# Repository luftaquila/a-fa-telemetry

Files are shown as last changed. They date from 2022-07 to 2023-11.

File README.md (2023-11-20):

# 차량 원격 계측 시스템

> [!CAUTION]
> ⚠️ DEPRECATED<br><br>
> 이 저장소는 유지보수되지 않습니다.<br><br>
> 추가 업데이트 및 유지보수는 오픈소스 DIY 데이터로거 [monolith](https://github.com/luftaquila/monolith)에서 이루어지고 있습니다.

<hr>

상위 프로젝트: [luftaquila/a-fa-landing](https://github.com/luftaquila/a-fa-landing)

아주대학교 자작자동차소학회 A-FA의 E-Formula 차량용 데이터로거입니다.

### 기능
1. CAN 버스 트래픽 모니터링 (BMS 및 모터 컨트롤러 데이터)
2. 6채널 디지털 입력 신호 모니터링 (BMS / BSPD / IMD 오류, HV 활성화, RTD 활성화 신호)
3. 4채널 아날로그 입력 신호 모니터링 (서스펜션 변위 센서)
4. 4채널 디지털 펄스 모니터링 (휠 스피드 센서)
5. 3축 가속도 센서 데이터(I2C)
6. GPS 위치 정보(UART)
7. 자체 CPU 온도 모니터링
8. 무선 시간 동기화 및 RTC를 통한 시간 정보 유지
9. 드라이버 계기판 LCD 시현(I2C)
10. 수집한 데이터의 SD카드 로깅(SDIO/FATFS)
11. 수집한 데이터의 실시간 무선 인터넷 전송

### 디렉터리 구조
* device: 임베디드 MCU 펌웨어
    * ECU: 차량 데이터 수집용 STM32F4 STM32CubeIDE 프로젝트
    * ESP: 서버 소켓 통신용 ESP32 아두이노 프로젝트
* server: 원격 계측 서버 백엔드(Node.js)
* web: 원격 계측 모니터링 웹 어플리케이션 프론트엔드

### 회로도 및 PCB
[설계 파일](https://github.com/luftaquila/a-fa-schematics/tree/master/PCBs/LV_PCB%20v2)




## 서비스 URL
* [A-FA E-포뮬러 원격 계측 시스템](https://a-fa.luftaquila.io/telemetry)

screencapture-a-fa-luftaquila-io-telemetry-2023-08-26-16_22_42



## Log structure (16 Byte)
```c
typedef struct {
  uint32_t timestamp;
  uint8_t level;
  uint8_t source;
  uint8_t key;
  uint8_t _reserved;
  uint8_t value[8];
} LOG;
```

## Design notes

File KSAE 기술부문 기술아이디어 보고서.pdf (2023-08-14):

자동차공학은 한국의 힘! | 사단법인 한국자동차공학회

## 대학생 자작자동차대회

# 기술부문 신청서

학교명 | 아주대학교 | 팀명 | A-FA
지도교수 | 전용호 | 팀장 | 김병찬
차량 | 명칭 | A12
| 제원 | 길이 mm × 폭 mm × 높이 mm (무게 kg)
부문 | | ■ 기술아이디어 부문 □ 디자인 부문

상기 참가팀은 KSAE 대학생 자작자동차대회의 기술부문 (기술아이디어 및 디자인) 참가를 신청하며 다음과 같이 보고서를 제출합니다.

년 | 월 | 일

# 대학생 자작자동차대회 조직위원회 귀중

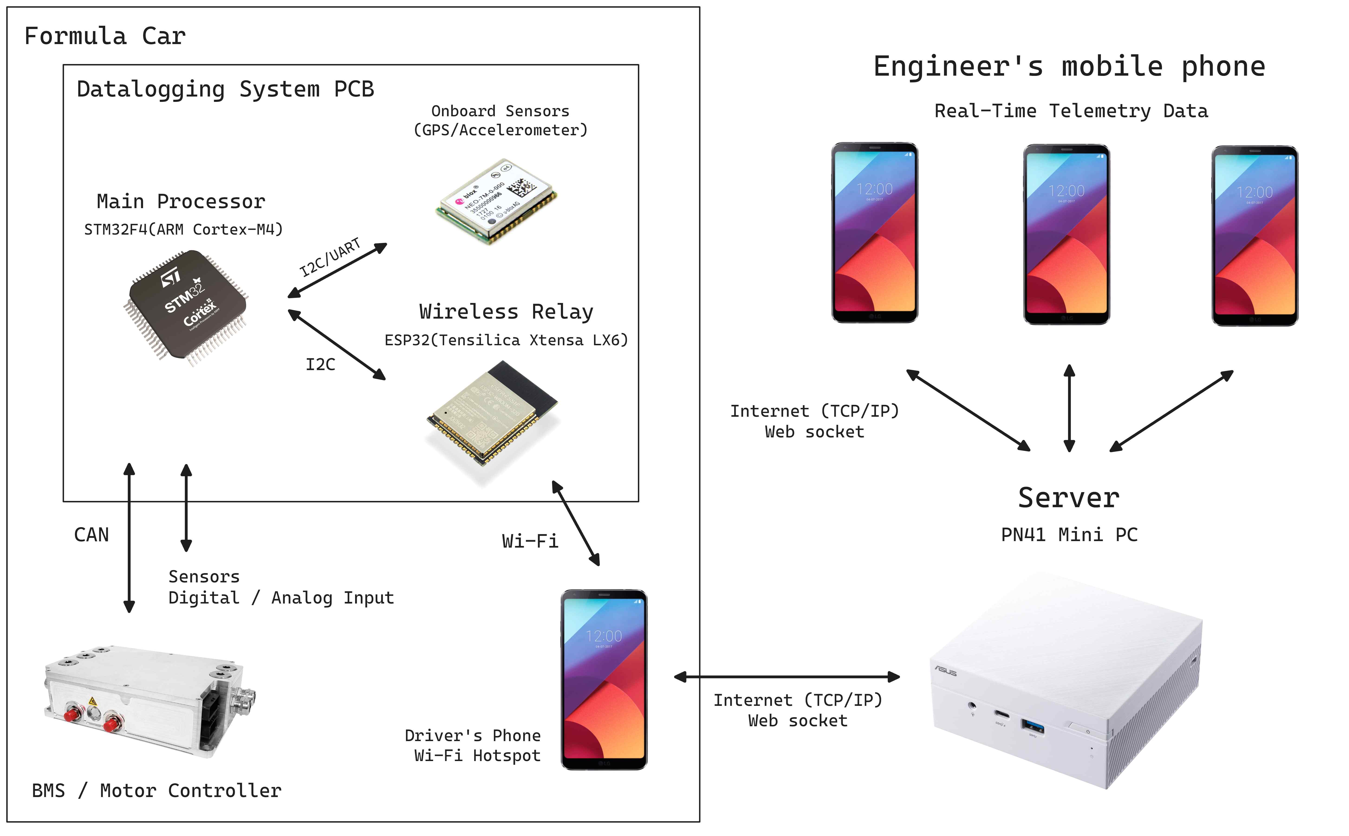
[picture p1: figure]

자동차공학은 한국의 힘! | 사단법인 한국자동차공학회

## 대학생 자작자동차대회

# 기술아이디어 보고서

￭ Summary
본 기술아이디어는 E-Formula 경주 차량의 주행 데이터 수집 및 실시간 원격 모니터링을 위한 임베디 드 하드웨어 및 소프트웨어 시스템이다. KSAE 출전과 같이 특수한 목적을 위해 개발하는 프로토타입 차량들은 제작 후 주행 성능 평가가 개발

과정에서 굉장히 큰 비중을 차지한다. 또한, 주행 중 예상치 못한 상황과 사고가 발생할 확률이 양산 차 량보다 훨씬 높다. 이러한 이유로 성능 평가, 사고 원인 분석 및 엔지니어링 등을 위해 차량의 주행 데 이터 수집은 반드시 필요하다. 그러나, 현재 찾아볼 수 있는 차량 데이터로깅 장비들은 그 성능과 기능 이 파편화되어 있어 하나의 장비로 개발팀의 모든 요구사항을 만족시키기 어렵다. 따라서, 하나의 데이 터로깅 플랫폼에서 CAN 트래픽, Real-Time Clock, 아날로그 / 디지털 입력, Pulse Capture, 가속도, GPS 정보 등 기술팀이 필요로 하는 모든 계측 데이터를 제공하여 이러한 문제를 해결할 수 있도록 한다. 또한, 본 대회처럼 사고 위험이 상존하는 주행 환경에서는 SD카드 소실, 데이터 유실 등으로 데이터에

접근할 수 없는 상황이 발생하기 쉽다. 이러한 상황에서도 데이터를 사후에 분석할 수 있도록 수집 즉시 무선으로 서버에 전송하여 데이터 확보를 보장한다. 서버는 전송된 데이터를 DB에 저장하는 동시에 웹 클라이언트에 중계하여 기술팀이 주행 중에도 차량의 데이터를 실시간으로 확인할 수 있도록 한다. ￭ Conceptual Design

자동차공학은 한국의 힘! | 사단법인 한국자동차공학회

별도로 설계한 PCB를 차량에 탑재하여 차량에서 각종 정보를 수집하고, 이를 SD카드에 저장하는 동시 에 무선 통신으로 서버에 전송한다. 드라이버는 차량 탑승 시 Wi-Fi Hotspot 기능을 활성화한 자신의 스 마트폰을 휴대하여 무선 전송이 가능하도록 인터넷 연결을 제공한다. 서버는 수신한 데이터를 해석하여 데이터베이스에 저장하며, 웹 클라이언트에 중계한다. 웹 클라이언트는 데이터를 그래픽 인터페이스를 제공하여 기술팀 엔지니어가 데이터를 한 눈에 손쉽게 확인할 수 있도록 하며, 언제 어디서나 접속할 수 있도록 인터넷 웹 페이지를 제공한다.

￭ Preliminary Design
하나의 데이터로깅 플랫폼으로 차량에서 다음과 같은 기능을 수행한다. 1. CAN 버스 트래픽 모니터링 (배터리 관리 시스템(BMS) 및 모터 컨트롤러 데이터 수집)
2. 6채널 디지털 입력 신호 모니터링 (BMS / BSPD / IMD 오류, HV 활성화, RTD 활성화 신호 수집)
3. 4채널 아날로그 입력 신호 모니터링 (서스펜션 변위 측정 센서 신호 등 수집)
4. 4채널 디지털 펄스 모니터링 (휠 회전 속도 측정 센서 신호 등 수집)
5. 3축 가속도 변화 모니터링
6. GPS 위치 정보 모니터링
7. 자체 CPU 온도 모니터링
8. 무선 시간 동기화 및 RTC(Real-Time Clock)을 통한 시간 정보 유지
9. 드라이버 계기판 LCD 시현 (CAN으로 수집한 속도 및 배터리 잔량 정보 등)
10. 수집한 데이터의 SD카드 로깅
11. 수집한 데이터의 무선 인터넷 전송

각 데이터는 최소 1Hz에서 최대 125Hz 주기로 생성된다. 종합하면 매 초에 약 120개의 로그가 발생한 다. 이를 모두 놓치지 않고 기록하기 위해 고성능 프로세서를 사용한다. ￭ Detail Design

메인 프로세서는 초당 수백 개씩 발생하는 로그를 모두 놓치지 않고 기록할 수 있도록 168MHz 클럭 으로 동작하는 32-bit MCU인 STM32F4를 채택하였다. 또한, 펌웨어를 C로 작성하여 시스템 메모리에 바 로 접근해 메모리 관리 오버헤드를 최대한 제거하였다. 메인 프로세서가 수집한 데이터는 I2C 통신을 통해 무선통신용 MCU인 ESP32로 전송된다. 기존에는

115200bps UART 통신을 통해 ASCII 문자열로 구성된 수백 Byte 크기의 로그를 전송하였다. 그러나 로 그 발생량이 많고 UART 통신 속도가 느려 STM32와 ESP32 간 통신에서 병목이 심하게 발생하였다. 이 에 로그 프로토콜을 별도로 정의하여 로그의 크기를 개당 16 Byte로 고정하였으며, I2C 400kHz Fast-Mode 통신을 통해 전송률을 3배 이상 개선하였다. 이를 통하여 초당 2500개 이상의 로그를 전송 할 수 있는 대역폭을 확보하였다.

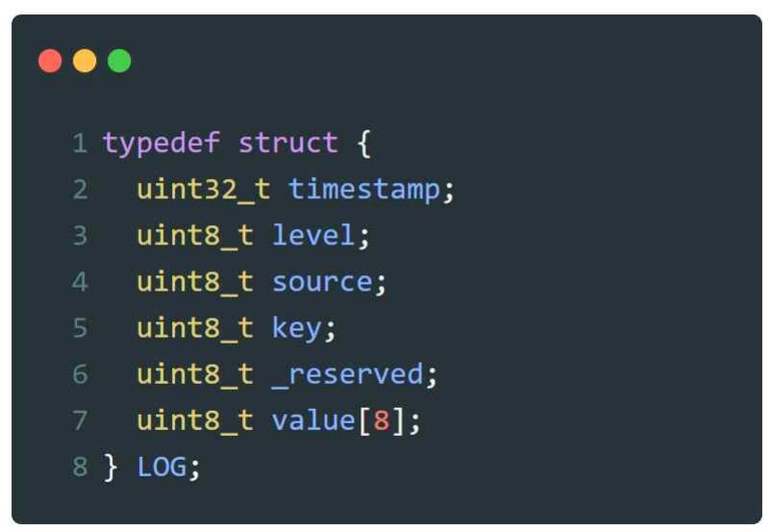
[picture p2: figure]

자동차공학은 한국의 힘! | 사단법인 한국자동차공학회

로그 구조는 다음과 같다. 로그 프로토콜의 세부 스펙은 여기에서 확인할 수 있다. (https://github.com/luftaquila/a-fa-telemetry/blob/master/device/ECU%20v2/Core/Inc/logger.h)

ESP32는 드라이버가 휴대하고 탑승한 스마트폰의 Wi-Fi 핫스팟 네트워크를 통해 무선으로 인터넷에 연결된다. STM32 프로세서로부터 I2C를 통해 전달받은 로그를 서버로 전달한다. 통신에는 웹 소켓을 사 용하여 HTTP 사용 시 발생하는 매 transaction에서의 TCP handshake 오버헤드 없이 실시간 양방향 통 신을 수행한다. 연결 실패나 통신 지연이 많이 발생할 수 있는 Wi-Fi 무선 통신의 특성을 고려하여, 무 선 연결 기능이 메인 프로세서의 데이터로깅을 방해하지 않도록 메인 프로세서와 무선통신만을 담당하 는 MCU를 분리하여 구현하였다. ESP32 또한 240MHz로 동작하는 고성능 2코어 프로세서로, 복잡한 WLAN 드라이버를 구동하여 로그

트래픽을 고속으로 발생시킬 수 있는 성능을 갖추고 있다. 또한, 펌웨어의 메인 코드를 실행하는 코어와 I2C 및 WLAN 수신 인터럽트 이벤트가 발생하는 코어를 분리하여 처리 성능을 극대화하였다. 펌웨어는 C++로 작성하였다. 이러한 16 Byte의 로그는 바이너리 형식으로 사람이 읽을 수 없다. 서버는 이러한 로그 메시지를 수신

하여 프로토콜에 맞게 해석하고 데이터베이스에 저장한다. 또한, 서버에 연결된 웹 클라이언트에 수신한 로그를 중계한다. 서버 코드는 Node.js로 작성하였으며, Ubuntu Server 22.04 LTS 환경의 홈 서버에서 실행된다. 또한, 서버 시간을 임베디드 장비에 전달하여 메인 프로세서의 RTC 유닛을 동기화한다. 이를 통하여 STM32가 항상 최신 시간을 유지할 수 있도록 해 로그의 활용성을 높인다. 마지막으로 웹 클라이언트는 위의 서버와 동일한 홈 서버에서 실행되는 NGINX 웹 서버가 서비스한다. 웹 클라이언트는 URL(https://a-fa.luftaquila.io/telemetry/)을 통하여 기술팀 각 인원이 자신의 스마트폰으

로 접근할 수 있으며, 주행 중 실시간으로 확인해야 하는 차량의 주요 지표를 시현한다. 최근 1분 추세 그래프를 제공하여 기술팀이 차량의 데이터 변화를 쉽게 파악할 수 있도록 시각화한다. 또한, 주행 후 SD 카드에 저장된 바이너리 형식의 데이터를 해석하여 읽을 수 있는 JSON, CSV 형식으로 변환하고 다 운로드하는 기능도 제공한다. 사용자 인터페이스는 다음과 같다.

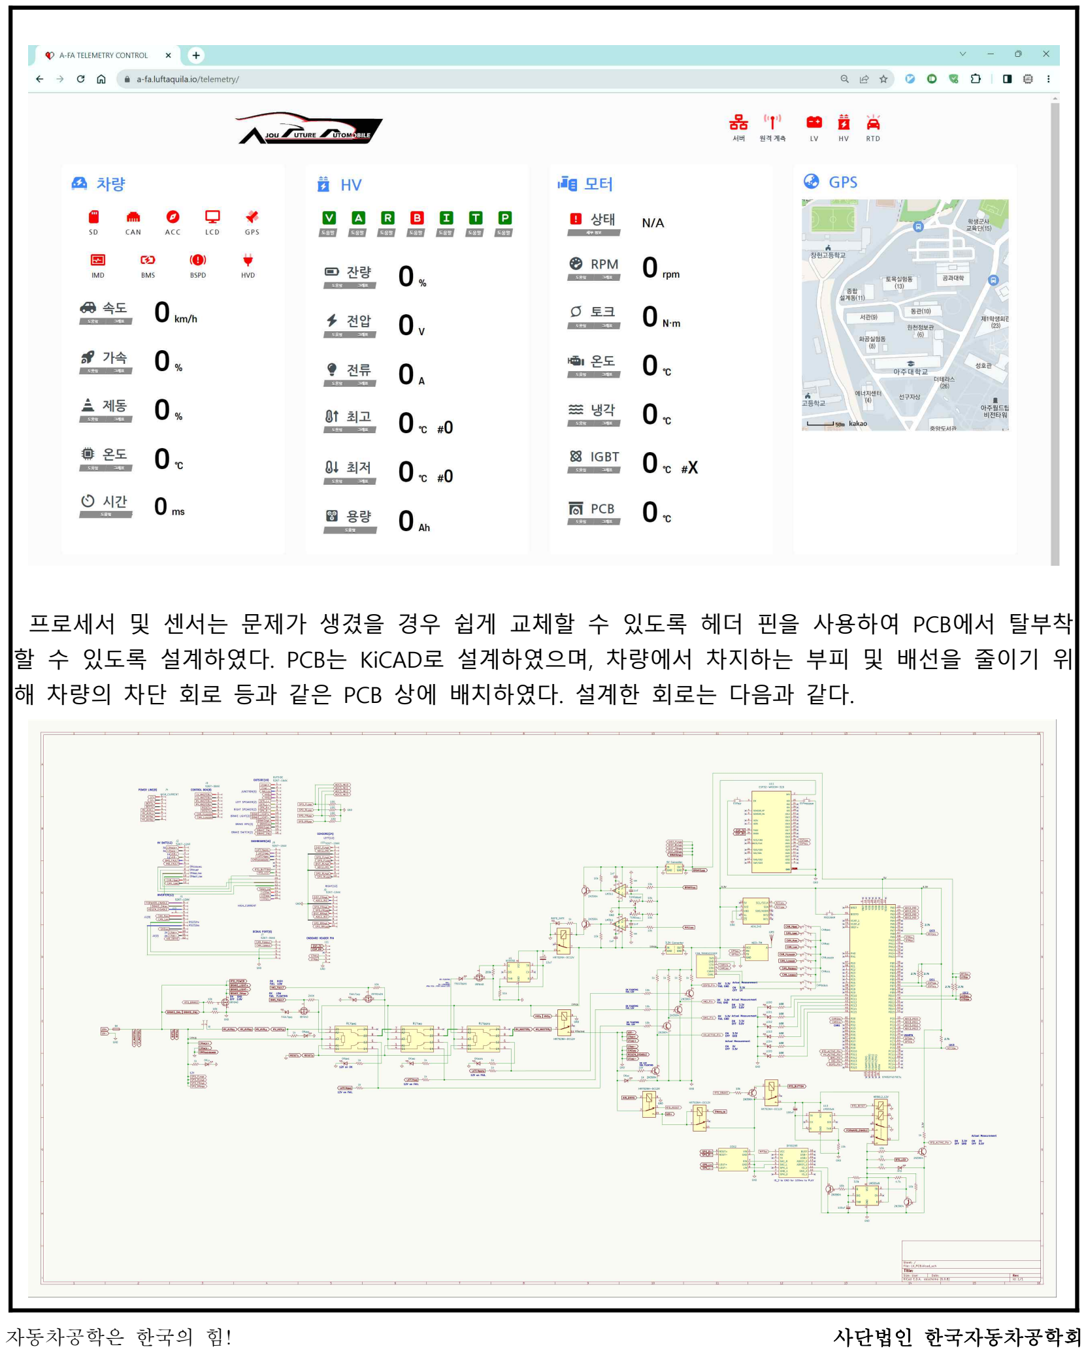
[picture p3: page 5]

자동차공학은 한국의 힘! | 사단법인 한국자동차공학회

프로세서 및 센서는 문제가 생겼을 경우 쉽게 교체할 수 있도록 헤더 핀을 사용하여 PCB에서 탈부착 할 수 있도록 설계하였다. PCB는 KiCAD로 설계하였으며, 차량에서 차지하는 부피 및 배선을 줄이기 위 해 차량의 차단 회로 등과 같은 PCB 상에 배치하였다. 설계한 회로는 다음과 같다.

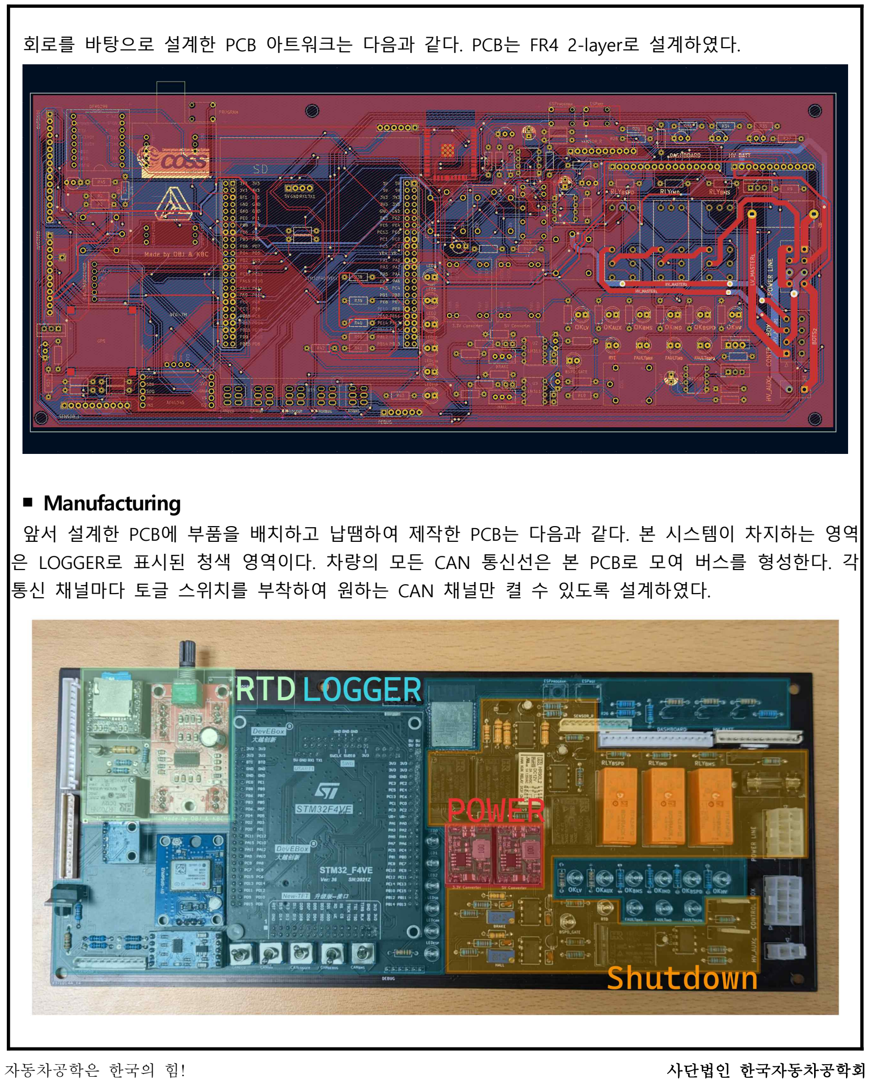
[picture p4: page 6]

자동차공학은 한국의 힘! | 사단법인 한국자동차공학회

회로를 바탕으로 설계한 PCB 아트워크는 다음과 같다. PCB는 FR4 2-layer로 설계하였다.

￭ Manufacturing
앞서 설계한 PCB에 부품을 배치하고 납땜하여 제작한 PCB는 다음과 같다. 본 시스템이 차지하는 영역 은 LOGGER로 표시된 청색 영역이다. 차량의 모든 CAN 통신선은 본 PCB로 모여 버스를 형성한다. 각 통신 채널마다 토글 스위치를 부착하여 원하는 CAN 채널만 켤 수 있도록 설계하였다.

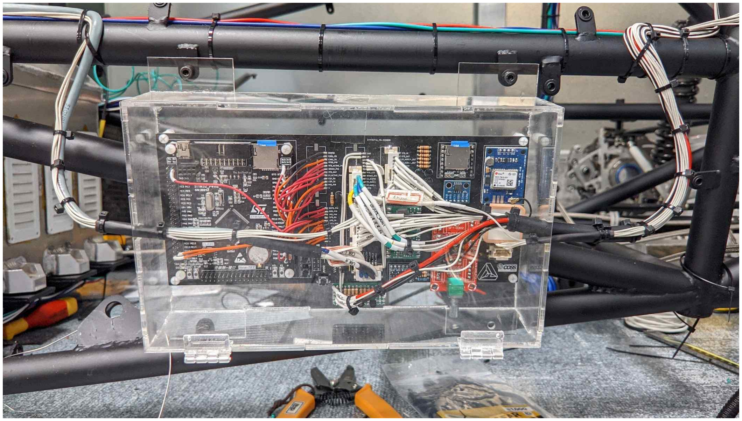
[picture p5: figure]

자동차공학은 한국의 힘! | 사단법인 한국자동차공학회

￭ Conclusion
데이터로깅 자체는 이미 많은 팀들이 필요성을 느끼고 각자 상용품 또는 자체 개발한 데이터로거를 사 용하고 있다. 그러나 본 기술아이디어는 하나의 플랫폼에서 CAN, 아날로그 및 디지털, 펄스 등 외부 신 호를 수집하며, 자체 GPS 및 가속도 센서, RTC 기능을 지원하고 수집한 로그를 SD카드에 저장하는 동 시에 무선으로 송신하여 기술팀 인원 전체가 자신의 스마트폰으로 실시간 주행 정보를 확인할 수 있는 강력한 기능을 제공하여 기존의 데이터로깅 시스템들과 차별점을 두었다. 또한, 개발한 임베디드 펌웨어, 서버 및 클라이언트 소스코드 등을 모두 공개하여 오픈소스 생태계에 기여하고 다른 팀에서도 자유롭게

사용할 수 있도록 하였다. (https://github.com/luftaquila/a-fa-telemetry)

￭ Acknowledgments
본 시스템은 올해 개발중인 차량에 탑재될 예정으로, 아직 완성된 차량에 탑재되어 주행하지 않았다. 그러나, 올해 개선 사항을 반영하지 않은 기존 시스템은 차량에 탑재되어 실제 주행에 사용하였다.

본 기술아이디어의 실제 적용 영상은 다음과 같다. 1. 시스템 작동 영상 1 (주행성능시험): https://www.youtube.com/watch?v=kZxLHQo4KEE

2. 시스템 작동 영상 2 (주행성능시험): https://www.youtube.com/watch?v=0vMqdhWlWpU
3. 시스템 작동 영상 3 (모터 구동 시험): https://www.youtube.com/watch?v=ZjLUNqeKCdc
4. 시스템 작동 영상 4 (모터 구동 시험): https://www.youtube.com/watch?v=fWfDaCTimpo

￭ References

1. RM0090 STM32F4 advanced Arm®-based 32-bit MCUs Reference Manual, STMicroelectronics.
2. ESP32 Technical Reference Manual Version 4.9, Espressif Systems, 2023.
3. ADXL345 Digital Accelerometer Datasheet Rev. G, Analog Devices, Inc., 2022.
4. NEO-7 u-blox 7 GNSS modules Data Sheet, U-BLOX.
5. Introduction to the Controller Area Network(CAN) Application Report, Texas Instruments, 2016.

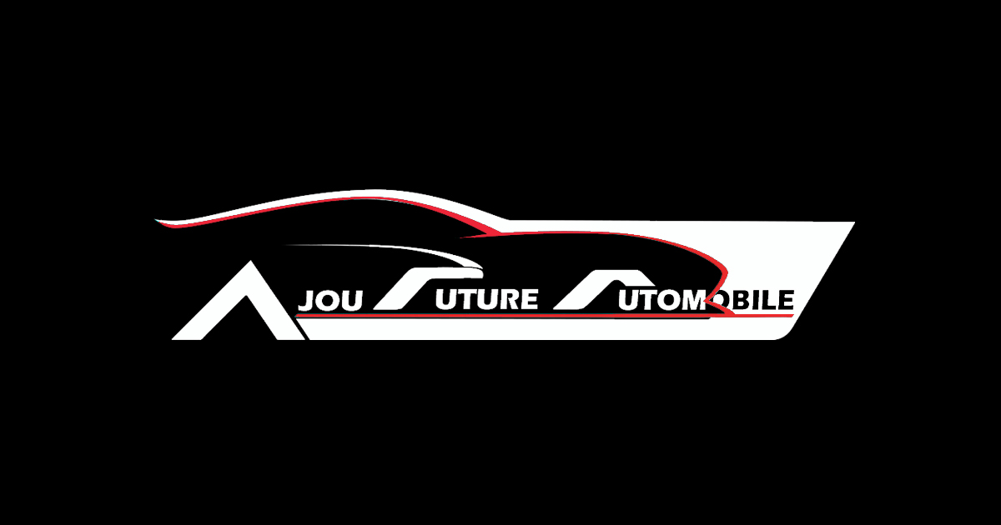
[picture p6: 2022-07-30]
web/assets/A-FA.jpeg

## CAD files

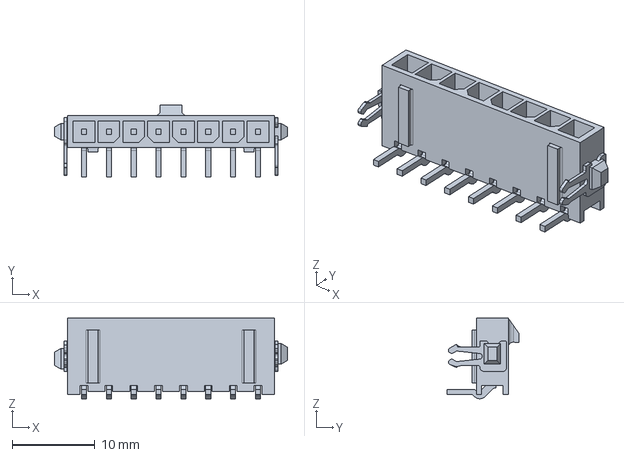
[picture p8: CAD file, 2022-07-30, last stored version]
schematics/PARTS/2-1445088-8/2-1445088-8.step
28.1 x 8.72 x 9.73 mm

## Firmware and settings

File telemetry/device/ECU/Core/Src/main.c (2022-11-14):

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
/* Includes ------------------------------------------------------------------*/
#include "main.h"
#include "adc.h"
#include "can.h"
#include "dma.h"
#include "fatfs.h"
#include "i2c.h"
#include "rtc.h"
#include "sdio.h"
#include "tim.h"
#include "usart.h"
#include "gpio.h"

/* USER CODE BEGIN Includes */
#include <stdio.h>
#include <stdlib.h>
#include <stdbool.h>
#include <string.h>
#include <inttypes.h>
#include <time.h>

#include "ringbuffer.h"
/* USER CODE END Includes */

/* USER CODE BEGIN PTD */
typedef struct {
	uint8_t* component;
	uint8_t* level;
	uint8_t* key;
	uint8_t* value;
} log_t;

typedef struct {
	uint8_t* name;
	uint32_t value;
	GPIO_TypeDef* port;
	uint16_t pin;
} GPIO_t;

typedef enum {
	LV_ACTIVE = 0,
	RTD = 1,
	BRAKE = 2,
	IMD = 3,
	BMS = 4,
	BSPD = 5,
	HVD = 6
} GPIO_INPUT_t;

typedef enum {
	GPS_TIME = 0,
	GPS_VALID,
	LAT,
	LAT_DIR,
	LON,
	LON_DIR,
	GROUND_SPEED,
	TRACK_ANGLE,
	GPS_DATE,
	COMPASS,
	COMPASS_DIR
} GPRMC_t;

typedef enum {
	CAN_BMS_CORE = 0,
	CAN_BMS_TEMP,
	CAN_INV_TEMP_1,
	CAN_INV_TEMP_3,
	CAN_INV_ANALOG_IN,
	CAN_INV_MOTOR_POS,
	CAN_INV_CURRENT,
	CAN_INV_VOLTAGE,
	CAN_INV_FLUX,
	CAN_INV_REF,
	CAN_INV_STATE,
	CAN_INV_FAULT,
	CAN_INV_TORQUE,
	CAN_INV_FLUX_WEAKING
} CAN_MSG_t;

typedef enum {
	CAN_BMS_CORE_ID = 0x6B0,
	CAN_BMS_TEMP_ID = 0x6B1,
	CAN_INV_TEMP_1_ID = 0xA0,
	CAN_INV_TEMP_3_ID = 0xA2,
	CAN_INV_ANALOG_IN_ID = 0xA3,
	CAN_INV_MOTOR_POS_ID = 0xA5,
	CAN_INV_CURRENT_ID = 0xA6,
	CAN_INV_VOLTAGE_ID = 0xA7,
	CAN_INV_FLUX_ID = 0xA8,
	CAN_INV_REF_ID = 0xA9,
	CAN_INV_STATE_ID = 0xAA,
	CAN_INV_FAULT_ID = 0xAB,
	CAN_INV_TORQUE_ID = 0xAC,
	CAN_INV_FLUX_WEAKING_ID = 0xAD
} CAN_MSG_ID_t;
/* USER CODE END PTD */

/* USER CODE BEGIN PD */
#define DEBUG_MODE 1
#define GPS_DEBUG 0

#define INPUT_GPIO_COUNT 7
#define CAN_MSG_COUNT 14

// ADC temperature sensor calibration values
#define TS_CAL1 *((uint16_t*)0x1FFF7A2C)
#define TS_CAL2 *((uint16_t*)0x1FFF7A2E)

// I2C
#define LCD_I2C_ADDRESS 0x27 << 1
#define ACC_I2C_ADDRESS 0x53 << 1

/* USER CODE END PD */


/* USER CODE BEGIN PV */

// error handler log
log_t errlog;

// SD file system;
FATFS SDFatFs;

// boot RTC time
uint64_t boot;
uint8_t logfile[30];
uint32_t isRTCFixed = false;

uint32_t isGPSFixed = false;

// 64KB log buffer
ring_buffer_t logbuffer;

// GPS UART6 receive buffer
uint8_t gps_rxd;
uint8_t gps_rxs[120];
uint32_t gps_valid = false;

// WiFi UART3 receive buffer
uint8_t wifi_rxd;
uint8_t wifi_rxs[50];
uint32_t wifi_valid = false;

// GPIO status
GPIO_t GPIO[8] = {
		{ .name = "HV",    .value = false, .port = GPIOD, .pin = LV_ACTIVE_Pin },
		{ .name = "RTD",   .value = false, .port = GPIOD, .pin = RTD_Pin },
		{ .name = "BRAKE", .value = false, .port = GPIOD, .pin = BRAKE_Pin },
		{ .name = "IMD",   .value = false, .port = GPIOD, .pin = IMD_Pin },
		{ .name = "BMS",   .value = false, .port = GPIOD, .pin = BMS_Pin },
		{ .name = "BSPD",  .value = false, .port = GPIOD, .pin = BSPD_Pin },
		{ .name = "HVD",   .value = false, .port = GPIOD, .pin = HVD_Pin }
};

// ADC temperature value
uint32_t adc_valid = false;
uint32_t core_temperature;

// GPIO check
uint32_t gpio_valid = false;

// LCD update flag
uint32_t lcd_valid = false;

// CAN receiver config
CAN_RxHeaderTypeDef can_rxh;
uint8_t can_rxb[8];
uint8_t can_rxd[CAN_MSG_COUNT][8];
uint32_t can_valid[CAN_MSG_COUNT] = { false, };
uint32_t can_active = false;
uint8_t *can_msg_id[CAN_MSG_COUNT] = { "CAN_BMS_CORE", "CAN_BMS_TEMP", "CAN_INV_TEMP_1", "CAN_INV_TEMP_3",
						   	   	   	   "CAN_INV_ANALOG_IN", "CAN_INV_MOTOR_POS", "CAN_INV_CURRENT", "CAN_INV_VOLTAGE",
									   "CAN_INV_FLUX", "CAN_INV_REF", "CAN_INV_STATE", "CAN_INV_FAULT",
									   "CAN_INV_TORQUE", "CAN_INV_FLUX_WEAKING" };

// SD mount flag
uint32_t sd_valid = false;

// Accelerometer data
uint8_t acc_rxd[6];
uint8_t acc_valid = false;

/* USER CODE END PV */

void SystemClock_Config(void);
/* USER CODE BEGIN 0 */
int _write(int file, uint8_t *ptr, int len) {
   HAL_UART_Transmit(&huart1, (uint8_t *)ptr, (uint16_t)len, 100);
   return (len);
}

uint64_t getDateTimeBits() {
	uint64_t result = 0;

	RTC_DateTypeDef sDate;
	RTC_TimeTypeDef sTime;

	HAL_RTC_GetTime(&hrtc, &sTime, FORMAT_BIN);
	HAL_RTC_GetDate(&hrtc, &sDate, FORMAT_BIN);

	result |= (uint64_t)(sTime.SubSeconds);
	result |= (uint64_t)(sTime.Seconds) << 8;
	result |= (uint64_t)(sTime.Minutes) << 16;
	result |= (uint64_t)(sTime.Hours) << 24;
	result |= (uint64_t)(sDate.Date) << 32;
	result |= (uint64_t)(sDate.Month) << 40;
	result |= (uint64_t)(sDate.Year) << 48;

	return result;
}


void SD_Setup() {
	// INIT & MOUNT
	disk_initialize((BYTE) 0);
	uint32_t err = f_mount(&SDFatFs, "", 0);

	#if DEBUG_MODE
		printf("mount err: %d\n", err);
	#endif
	if(err != FR_OK) {
		errlog.component = "ECU";
		errlog.level = "ERRR";
		errlog.key = "SD";
		errlog.value = malloc(17);
		sprintf(errlog.value, "SD_MOUNT_ERR: %d", err);

		Error_Handler();
		free(errlog.value);
	}

	sd_valid = true;

	log_t log;
	log.component = "ECU";
	log.level = "INFO";
	log.key = "SD";
	log.value = "SD_MOUNTED";
	LOGGER(&log);
}


uint8_t* log_string_generator(log_t* log, uint8_t* str, uint32_t* logsize) {
	uint64_t timestamp = getDateTimeBits();

	// set log content
	sprintf(str, "![%s]\t[20%d-%02d-%02d %02d:%02d:%02d.%03d]\t%s\t\t%s\t\t\t%s\n",
			log->level,
			(uint32_t)(timestamp >> 48), (uint32_t)(timestamp << 16 >> 56), (uint32_t)(timestamp << 24 >> 56),
			(uint32_t)(timestamp << 32 >> 56), (uint32_t)(timestamp << 40 >> 56), (uint32_t)(timestamp << 48 >> 56), (int)(999.0 / 255.0 * (float)(255 - (timestamp << 56 >> 56))),
			log->component, log->key, log->value);

	*logsize = strlen(str);
	return str;
}

void LOGGER(log_t* log) {
	uint8_t* content = malloc(100);
	uint32_t logsize;

	log_string_generator(log, content, &logsize);

	// append log to buffer
	ring_buffer_queue_arr(&logbuffer, content, logsize + 1);

	#if DEBUG_MODE
		printf("LOG: %s", content);
	#endif

	// mount SD
	if (!sd_valid) {
		SD_Setup();
	}

	// SAVE TO SD
	FIL file;
	uint32_t writtenBytesCount;

	// OPEN FILE
	uint32_t err = f_open(&file, logfile, FA_OPEN_APPEND | FA_WRITE);
	#if DEBUG_MODE
		printf("sd open: %d, %s\n", err, logfile);
	#endif
	if (err != FR_OK) {
		errlog.component = "ECU";
		errlog.level = "ERRR";
		errlog.key = "SD";
		errlog.value = malloc(16);
		sprintf(errlog.value, "SD_OPEN_ERR: %d", err);

		Error_Handler();
		free(errlog.value);
	}

	// WRITE TO FILE
	err = f_write(&file, content, logsize, (void *)&writtenBytesCount);
	#if DEBUG_MODE
		printf("sd write: %d, %s, %d\n", err, logfile, writtenBytesCount);
	#endif
	if (err != FR_OK) {
		errlog.component = "ECU";
		errlog.level = "ERRR";
		errlog.key = "SD";
		errlog.value = malloc(17);
		sprintf(errlog.value, "SD_WRITE_ERR: %d", err);

		Error_Handler();
		free(errlog.value);
	}

	// CLOSE FILE
	err = f_close(&file);
	#if DEBUG_MODE
		printf("sd close: %d\n\n", err);
	#endif
	if(err != FR_OK) {
		errlog.component = "ECU";
		errlog.level = "ERRR";
		errlog.key = "SD";
		errlog.value = malloc(17);
		sprintf(errlog.value, "SD_CLOSE_ERR: %d", err);

		Error_Handler();
		free(errlog.value);
	}

	free(content);
}


/* ========== GPIO START ========== */
void Sensor_Setup() {
	// internal temperature sensor time
	HAL_TIM_Base_Start_IT(&htim4);

	// initialize APPS pin
	HAL_GPIO_WritePin(GPIOD, RTD_ACTIVE_Pin, GPIO_PIN_RESET);

	// initialize RTDS pin
	HAL_GPIO_WritePin(GPIOA, RTDS_Pin, GPIO_PIN_SET);

	// read initial GPIO states
	for (uint32_t i = 0; i < INPUT_GPIO_COUNT; i++) {
		GPIO[i].value = HAL_GPIO_ReadPin(GPIO[i].port, GPIO[i].pin);

		log_t log;
		log.component = "ECU";
		log.level = "INFO";
		log.key = "GPIO";
		log.value = malloc(strlen(GPIO[i].name) + 3);
		sprintf(log.value, "%s %d", GPIO[i].name, (GPIO[i].value));
		LOGGER(&log);
		free(log.value);
	}
}

void Sensor_Manager() {
	// detect GPIO state change
	for (uint32_t i = 0; i < INPUT_GPIO_COUNT; i++) {
		if (GPIO[i].value != HAL_GPIO_ReadPin(GPIO[i].port, GPIO[i].pin)) {
			log_t log;
			log.component = "ECU";
			log.level = "INFO";
			log.key = "GPIO";
			log.value = malloc(strlen(GPIO[i].name) + 3);
			sprintf(log.value, "%s %d", GPIO[i].name, !(GPIO[i].value));
			LOGGER(&log);
			free(log.value);

			GPIO[i].value = !(GPIO[i].value);
		}
	}

	// log GPIO state
	if (gpio_valid) {
		static uint32_t checkedGPIOcount = 0;
		static uint32_t gpioCheckStartTime = 0;
		if (!gpioCheckStartTime) gpioCheckStartTime = HAL_GetTick();

		if (HAL_GetTick() > gpioCheckStartTime + 100 * checkedGPIOcount) {
			GPIO[checkedGPIOcount].value = HAL_GPIO_ReadPin(GPIO[checkedGPIOcount].port, GPIO[checkedGPIOcount].pin);

			log_t log;
			log.component = "ECU";
			log.level = "INFO";
			log.key = "GPIO";
			log.value = malloc(strlen(GPIO[checkedGPIOcount].name) + 3);
			sprintf(log.value, "%s %d", GPIO[checkedGPIOcount].name, (GPIO[checkedGPIOcount].value));
			LOGGER(&log);
			free(log.value);

			checkedGPIOcount++;

			if (checkedGPIOcount == INPUT_GPIO_COUNT) {
				gpio_valid = false;
				checkedGPIOcount = 0;
				gpioCheckStartTime = 0;
			}
		}
	}

	// log internal temperature
	if (adc_valid) {
		log_t log;
		log.component = "ECU";
		log.level = "INFO";
		log.key = "TEMPERATURE";
		log.value = malloc(5);
		sprintf(log.value, "%d", core_temperature);
		LOGGER(&log);
		free(log.value);

		adc_valid = false;
	}
}
/* ========== GPIO END ========== */


void RTD_Manager() {
	static uint32_t RTD_FLAG = false;
	static uint32_t RTD_COUNTER_ACTIVE = false;

	static uint32_t RTD_TIMER;

	// read RTD related GPIO state
	uint32_t LV_ACTIVE    = HAL_GPIO_ReadPin(GPIOD, LV_ACTIVE_Pin);
	uint32_t RTD       	  = HAL_GPIO_ReadPin(GPIOD, RTD_Pin);
	uint32_t BRAKE        = HAL_GPIO_ReadPin(GPIOD, BRAKE_Pin);

	// on RTD condition
	if (!RTD_FLAG && LV_ACTIVE && RTD && BRAKE) {
	  // START RTD ACTIVATION TIMER
	  if (!RTD_COUNTER_ACTIVE) {
		 RTD_COUNTER_ACTIVE = true;
		 RTD_TIMER = HAL_GetTick();
	  }

	  // RTD ACTIVATION SEQUENCE
	  else if (HAL_GetTick() - RTD_TIMER > 1000) {
		 // Mark RTD active
		 RTD_FLAG = true;

		 // Play RTDS
		 HAL_GPIO_WritePin(GPIOA, RTDS_Pin, GPIO_PIN_RESET);
		 HAL_TIM_Base_Start_IT(&htim2);

		 // Activate APPS relay and RTD indicator LED
		 HAL_GPIO_WritePin(GPIOD, RTD_ACTIVE_Pin, GPIO_PIN_SET);

		 log_t log;
		 log.component = "ECU";
		 log.level = "INFO";
		 log.key = "RTD";
		 log.value = malloc(10);
		 sprintf(log.value, "%d", HAL_GetTick());
		 LOGGER(&log);
		 free(log.value);
	  }
	}
	// RTD abort
	else {
	  RTD_COUNTER_ACTIVE = false;
	}
}


/* ========== CAN RECEIVER START ========== */
void CAN_Setup() {
   CAN_FilterTypeDef CAN_Filter_Config;

   CAN_Filter_Config.FilterBank = 0;
   CAN_Filter_Config.FilterMode = CAN_FILTERMODE_IDMASK;
   CAN_Filter_Config.FilterScale = CAN_FILTERSCALE_32BIT;
   CAN_Filter_Config.FilterIdHigh = 0x0000;
   CAN_Filter_Config.FilterIdLow = 0x0000;
   CAN_Filter_Config.FilterMaskIdHigh = 0x0000;
   CAN_Filter_Config.FilterMaskIdLow = 0x0000;
   CAN_Filter_Config.FilterFIFOAssignment = CAN_RX_FIFO0;
   CAN_Filter_Config.FilterActivation = ENABLE;
   CAN_Filter_Config.SlaveStartFilterBank = 14;

   // CAN configuration
   if (HAL_CAN_ConfigFilter(&hcan1, &CAN_Filter_Config) != HAL_OK) {
		errlog.component = "ECU";
		errlog.level = "ERRR";
		errlog.key = "CAN";
		errlog.value = malloc(25);
		sprintf(errlog.value, "HAL_CAN_ConfigFilter_ERR");

		Error_Handler();
		free(errlog.value);
   }

   // CAN start
   if (HAL_CAN_Start(&hcan1) != HAL_OK) {
		errlog.component = "ECU";
		errlog.level = "ERRR";
		errlog.key = "CAN";
		errlog.value = malloc(18);
		sprintf(errlog.value, "HAL_CAN_Start_ERR");

		Error_Handler();
		free(errlog.value);
   }

   // CAN RX notification activation
   if (HAL_CAN_ActivateNotification(&hcan1, CAN_IT_RX_FIFO0_MSG_PENDING) != HAL_OK) {
		errlog.component = "ECU";
		errlog.level = "ERRR";
		errlog.key = "CAN";
		errlog.value = malloc(61);
		sprintf(errlog.value, "HAL_CAN_ActivateNotification_CAN_IT_RX_FIFO0_MSG_PENDING_ERR");

		Error_Handler();
		free(errlog.value);
   }
   can_active = true;

   // CAN RX FULL notification activation
   if (HAL_CAN_ActivateNotification(&hcan1, CAN_IT_RX_FIFO0_FULL) != HAL_OK) {
		errlog.component = "ECU";
		errlog.level = "ERRR";
		errlog.key = "CAN";
		errlog.value = malloc(54);
		sprintf(errlog.value, "HAL_CAN_ActivateNotification_CAN_IT_RX_FIFO0_FULL_ERR");

		Error_Handler();
		free(errlog.value);
   }
}

void HAL_CAN_RxFifo0MsgPendingCallback(CAN_HandleTypeDef *CAN_Handle) {
	if (HAL_CAN_GetRxMessage(CAN_Handle, CAN_RX_FIFO0, &can_rxh, can_rxb) != HAL_OK) {
		errlog.component = "ECU";
		errlog.level = "ERRR";
		errlog.key = "CAN";
		errlog.value = malloc(25);
		sprintf(errlog.value, "HAL_CAN_GetRxMessage_ERR");

		Error_Handler();
		free(errlog.value);
	}

#if DEBUG_MODE
	printf("CAN: %x 0x%02X 0x%02X 0x%02X 0x%02X 0x%02X 0x%02X 0x%02X 0x%02X\n", can_rxh.StdId, can_rxb[0], can_rxb[1], can_rxb[2], can_rxb[3], can_rxb[4], can_rxb[5], can_rxb[6], can_rxb[7]);
#endif

	switch (can_rxh.StdId) {
		case CAN_BMS_CORE_ID:
			memcpy(can_rxd[CAN_BMS_CORE], can_rxb, 8);
			can_valid[CAN_BMS_CORE] = true;
			break;

		case CAN_BMS_TEMP_ID:
			memcpy(can_rxd[CAN_BMS_TEMP], can_rxb, 8);
			can_valid[CAN_BMS_TEMP] = true;
			break;

		case CAN_INV_TEMP_1_ID:
			memcpy(can_rxd[CAN_INV_TEMP_1], can_rxb, 8);
			can_valid[CAN_INV_TEMP_1] = true;
			break;

		case CAN_INV_TEMP_3_ID:
			memcpy(can_rxd[CAN_INV_TEMP_3], can_rxb, 8);
			can_valid[CAN_INV_TEMP_3] = true;
			break;

		case CAN_INV_ANALOG_IN_ID:
			memcpy(can_rxd[CAN_INV_ANALOG_IN], can_rxb, 8);
			can_valid[CAN_INV_ANALOG_IN] = true;
			break;

		case CAN_INV_MOTOR_POS_ID:
			memcpy(can_rxd[CAN_INV_MOTOR_POS], can_rxb, 8);
			can_valid[CAN_INV_MOTOR_POS] = true;
			break;

		case CAN_INV_CURRENT_ID:
			memcpy(can_rxd[CAN_INV_CURRENT], can_rxb, 8);
			can_valid[CAN_INV_CURRENT] = true;
			break;

		case CAN_INV_VOLTAGE_ID:
			memcpy(can_rxd[CAN_INV_VOLTAGE], can_rxb, 8);
			can_valid[CAN_INV_VOLTAGE] = true;
			break;

		case CAN_INV_FLUX_ID:
			memcpy(can_rxd[CAN_INV_FLUX], can_rxb, 8);
			can_valid[CAN_INV_FLUX] = true;
			break;

		case CAN_INV_REF_ID:
			memcpy(can_rxd[CAN_INV_REF], can_rxb, 8);
			can_valid[CAN_INV_REF] = true;
			break;

		case CAN_INV_STATE_ID:
			memcpy(can_rxd[CAN_INV_STATE], can_rxb, 8);
			can_valid[CAN_INV_STATE] = true;
			break;

		case CAN_INV_FAULT_ID:
			memcpy(can_rxd[CAN_INV_FAULT], can_rxb, 8);
			can_valid[CAN_INV_FAULT] = true;
			break;

		case CAN_INV_TORQUE_ID:
			memcpy(can_rxd[CAN_INV_TORQUE], can_rxb, 8);
			can_valid[CAN_INV_TORQUE] = true;
			break;

		case CAN_INV_FLUX_WEAKING_ID:
			memcpy(can_rxd[CAN_INV_FLUX_WEAKING], can_rxb, 8);
			can_valid[CAN_INV_FLUX_WEAKING] = true;
			break;
	}
}

void HAL_CAN_RxFifo0FullCallback(CAN_HandleTypeDef *CAN_Handle) {
	// deactivate CAN RX on FIFO FULL
	if (HAL_CAN_DeactivateNotification(&hcan1, CAN_IT_RX_FIFO0_MSG_PENDING) != HAL_OK) {
		errlog.component = "ECU";
		errlog.level = "ERRR";
		errlog.key = "CAN";
		errlog.value = malloc(63);
		sprintf(errlog.value, "HAL_CAN_DeactivateNotification_CAN_IT_RX_FIFO0_MSG_PENDING_ERR");

		Error_Handler();
		free(errlog.value);
	}
	can_active = false;
}

void CAN_Manager() {
	for (uint32_t i = 0; i < CAN_MSG_COUNT; i++) {
		if (can_valid[i]) {
			log_t log;
	        log.component = i < 2 ? "BMS" : "INV";
	        log.level = (i == 0 && (can_rxd[i][5] | can_rxd[i][6])) ? "ERRR" : "INFO";
	        log.key = can_msg_id[i];
			log.value = malloc(40);
			sprintf(log.value, "0x%02X 0x%02X 0x%02X 0x%02X 0x%02X 0x%02X 0x%02X 0x%02X", can_rxd[i][0], can_rxd[i][1], can_rxd[i][2], can_rxd[i][3], can_rxd[i][4], can_rxd[i][5], can_rxd[i][6], can_rxd[i][7]);
			LOGGER(&log);
			free(log.value);

			can_valid[i] = false;
		}
	}

	if (!can_active) {
		// CAN RX notification activation
		if (HAL_CAN_ActivateNotification(&hcan1, CAN_IT_RX_FIFO0_MSG_PENDING) != HAL_OK) {
			errlog.component = "ECU";
			errlog.level = "ERRR";
			errlog.key = "CAN";
			errlog.value = malloc(61);
			sprintf(errlog.value, "HAL_CAN_ActivateNotification_CAN_IT_RX_FIFO0_MSG_PENDING_ERR");

			Error_Handler();
			free(errlog.value);
		}
	}
}

void HAL_CAN_ErrorCallback(CAN_HandleTypeDef *hcan) {
	errlog.component = "ECU";
	errlog.level = "ERRR";
	errlog.key = "CAN";
	errlog.value = malloc(26);
	sprintf(errlog.value, "HAL_CAN_ErrorCallback_ERR");

	Error_Handler();
	free(errlog.value);
}
/* ========== CAN RECEIVER END ========== */


void HAL_UART_RxCpltCallback(UART_HandleTypeDef *huart) {
	// for GPS
	if(huart->Instance == USART6) {
		// process only if data is not ready
		if(gps_valid) return;
		else {
			// received character position
			static uint32_t len = 0;

			// if received data is line ending
			if(gps_rxd == '\n') {
				gps_rxs[len] = '\0';
				len = 0;

				// process only if received line is GPRMC
				if(strstr(gps_rxs, "$GPRMC")) {
					// set GPS data ready
					gps_valid = true;
					return;
				}
			}

			// append received byte to receive buffer
			else gps_rxs[len++] = gps_rxd;

			// re-enable UART interrupt
			HAL_UART_Receive_IT(&huart6, &gps_rxd, 1);
		}
	}

	// for WiFi
	else if(huart->Instance == USART3) {
		// process only if data is ready to processed
		if(wifi_valid) return;
		else {
			static uint32_t len = 0;

			if(wifi_rxd == '\n') {
				wifi_rxs[len] = '\0';
				len = 0;

				// set flag only if received line contains $ESP
				if(strstr(wifi_rxs, "$ESP")) {
					wifi_valid = true;
					return;
				}
			}

			else {
				// cut received buffer if len > 50
				if (len == 50) len = 0;
				wifi_rxs[len++] = wifi_rxd;
			}

			// re-enable UART interrupt
			HAL_UART_Receive_IT(&huart3, &wifi_rxd, 1);
		}
	}
}


/* ========== GPS RECEIVER START ========== */
void GPS_Setup() {
	/*
	const uint8_t NMEA_cmd[5][16] = {
		{ 0xB5, 0x62, 0x06, 0x01, 0x08, 0x00, 0xF0, 0x00, 0x00, 0x00, 0x00, 0x00, 0x00, 0x01, 0x00, 0x24 }, // disable GxGGA
		{ 0xB5, 0x62, 0x06, 0x01, 0x08, 0x00, 0xF0, 0x01, 0x00, 0x00, 0x00, 0x00, 0x00, 0x01, 0x01, 0x2B }, // disable GxGLL
		{ 0xB5, 0x62, 0x06, 0x01, 0x08, 0x00, 0xF0, 0x02, 0x00, 0x00, 0x00, 0x00, 0x00, 0x01, 0x02, 0x32 }, // disable GxGSA
		{ 0xB5, 0x62, 0x06, 0x01, 0x08, 0x00, 0xF0, 0x03, 0x00, 0x00, 0x00, 0x00, 0x00, 0x01, 0x03, 0x39 }, // disable GxGSV
		{ 0xB5, 0x62, 0x06, 0x01, 0x08, 0x00, 0xF0, 0x05, 0x00, 0x00, 0x00, 0x00, 0x00, 0x01, 0x05, 0x47 }  // disable GxVTG
	};

	HAL_UART_Transmit(&huart6, NMEA_cmd[0], 16, 50);
	HAL_UART_Transmit(&huart6, NMEA_cmd[1], 16, 50);
	HAL_UART_Transmit(&huart6, NMEA_cmd[2], 16, 50);
	HAL_UART_Transmit(&huart6, NMEA_cmd[3], 16, 50);
	HAL_UART_Transmit(&huart6, NMEA_cmd[4], 16, 50);
	*/

	const uint8_t UBX_rate_cmd[14] = { 0xB5, 0x62, 0x06, 0x08, 0x06, 0x00, 0xC8, 0x00, 0x01, 0x00, 0x01, 0x00, 0xDE, 0x6A }; // set update rate 5Hz
	const uint8_t UBX_power_cmd[16] = { 0xB5, 0x62, 0x06, 0x86, 0x08, 0x00, 0x00, 0x00, 0x00, 0x00, 0x00, 0x00, 0x00, 0x00, 0x94, 0x5A }; // set full power

	HAL_UART_Transmit(&huart6, UBX_rate_cmd, 14, 50);
	HAL_UART_Transmit(&huart6, UBX_power_cmd, 16, 50);

	// enable UART receive
	HAL_UART_Receive_IT(&huart6, &gps_rxd, 1);
}
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
int main(void)
{
  /* MCU Configuration--------------------------------------------------------*/

  /* Reset of all peripherals, Initializes the Flash interface and the Systick. */
  HAL_Init();

  /* Configure the system clock */
  SystemClock_Config();

  /* Initialize all configured peripherals */
  MX_GPIO_Init();
  MX_DMA_Init();
  MX_TIM2_Init();
  MX_USART1_UART_Init();
  MX_I2C2_Init();
  MX_SDIO_SD_Init();
  MX_RTC_Init();
  MX_FATFS_Init();
  MX_USART6_UART_Init();
  MX_USART3_UART_Init();
  MX_ADC1_Init();
  MX_TIM4_Init();
  MX_I2C1_Init();
  MX_TIM3_Init();
  MX_TIM12_Init();
  MX_CAN1_Init();
  /* USER CODE BEGIN 2 */

  // set boot time and log file name
  boot = getDateTimeBits();
  sprintf(logfile, "A-FA 20%d-%02d-%02d %02d-%02d-%02d.log",
		(uint32_t)(boot >> 48), (uint32_t)(boot << 16 >> 56), (uint32_t)(boot << 24 >> 56),
		(uint32_t)(boot << 32 >> 56), (uint32_t)(boot << 40 >> 56), (uint32_t)(boot << 48 >> 56));

  // initialize 32KB log buffer
  ring_buffer_init(&logbuffer);

  // set onboard LED active
  HAL_GPIO_WritePin(GPIOA, LED1_Pin, GPIO_PIN_RESET);
  HAL_GPIO_WritePin(GPIOA, LED2_Pin, GPIO_PIN_SET);

  // log system startup
  log_t log;
  log.component = "ECU";
  log.level = "INFO";
  log.key = "STARTUP";
  log.value = "STARTUP";
  LOGGER(&log);

  // set LCD
  LCD_Setup();

  // set WiFi
  HAL_UART_Receive_IT(&huart3, &wifi_rxd, 1);
  HAL_UART_Transmit(&huart3, "ESP CHECK", 10, 10);

  // initialize GPIOs
  Sensor_Setup();

  // set CAN
  CAN_Setup();

  // set accelerometer
  //ACC_Setup();

  // set GPS
  GPS_Setup();

  /* USER CODE END 2 */

  /* Infinite loop */
  /* USER CODE BEGIN WHILE */
  while (1) {
	RTD_Manager();
	Sensor_Manager();
	CAN_Manager();
	GPS_Manager();
	WiFi_Manager();
	LCD_Manager();
	//ACC_Manager();
    /* USER CODE END WHILE */

    /* USER CODE BEGIN 3 */
  }
  /* USER CODE END 3 */
}

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


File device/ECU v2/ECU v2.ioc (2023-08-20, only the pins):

Mcu.UserName=STM32F407VETx
PA0-WKUP.Signal=ADCx_IN0
PA1.Signal=ADCx_IN1
PA10.Signal=USART1_RX
PA2.Signal=ADCx_IN2
PA3.Signal=ADCx_IN3
PA6.GPIO_Label=LED00
PA6.Signal=GPIO_Output
PA7.GPIO_Label=LED01
PA7.Signal=GPIO_Output
PA8.Signal=I2C3_SCL
PA9.Signal=USART1_TX
PB0.Signal=S_TIM3_CH3
PB1.Signal=S_TIM3_CH4
PB10.Signal=I2C2_SCL
PB11.Signal=I2C2_SDA
PB12.GPIO_Label=SDIO_DETECT
PB12.Signal=GPIO_Input
PB6.Signal=I2C1_SCL
PB7.Signal=I2C1_SDA
PC10.Signal=UART4_TX
PC11.Signal=UART4_RX
PC12.Signal=SDIO_CK
PC14-OSC32_IN.Signal=RCC_OSC32_IN
PC15-OSC32_OUT.Signal=RCC_OSC32_OUT
PC8.Signal=SDIO_D0
PC9.Signal=I2C3_SDA
PD0.Signal=CAN1_RX
PD1.Signal=CAN1_TX
PD10.GPIO_Label=RTD_ACTIVE
PD10.Signal=GPIO_Input
PD11.GPIO_Label=HV_ACTIVE
PD11.Signal=GPIO_Input
PD12.GPIO_Label=BMS_FAULT
PD12.Signal=GPIO_Input
PD13.GPIO_Label=IMD_FAULT
PD13.Signal=GPIO_Input
PD14.GPIO_Label=BSPD_FAULT
PD14.Signal=GPIO_Input
PD2.Signal=SDIO_CMD
PD5.Signal=USART2_TX
PD6.Signal=USART2_RX
PE10.GPIO_Label=ERR_SYS
PE10.Signal=GPIO_Output
PE11.GPIO_Label=ERR_CAN
PE11.Signal=GPIO_Output
PE12.GPIO_Label=LED_HEARTBEAT
PE12.Signal=GPIO_Output
PE13.GPIO_Label=LED_SD
PE13.Signal=GPIO_Output
PE14.GPIO_Label=LED_CAN
PE14.Signal=GPIO_Output
PE15.GPIO_Label=LED_ESP
PE15.Signal=GPIO_Output
PH0-OSC_IN.Signal=RCC_OSC_IN
PH1-OSC_OUT.Signal=RCC_OSC_OUT

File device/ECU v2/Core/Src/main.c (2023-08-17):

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
/* Includes ------------------------------------------------------------------*/
#include "main.h"
#include "adc.h"
#include "can.h"
#include "dma.h"
#include "fatfs.h"
#include "i2c.h"
#include "rtc.h"
#include "sdio.h"
#include "tim.h"
#include "usart.h"
#include "gpio.h"

/* USER CODE BEGIN Includes */
#include "logger.h"
#include "string.h"
#include "stdlib.h"
/* USER CODE END Includes */

/* USER CODE BEGIN PD */
extern int32_t SYS_LOG(LOG_LEVEL level, LOG_SOURCE source, int32_t key);

extern inline uint32_t to_uint(uint8_t *str, char garbage);
extern inline uint32_t drop_point(uint8_t *str);
/* USER CODE END PD */


/* USER CODE BEGIN PV */
ERROR_CODE err;

// log data
FIL logfile;
LOG syslog;

// SD write buffer
ring_buffer_t LOG_BUFFER;
uint8_t LOG_BUFFER_ARR[1 << 12]; // 4KB

// system state log
SYSTEM_STATE sys_state;

// timer set flag
uint32_t timer_flag = 0;

// adc conversion flag and data
uint32_t adc_flag = 0;
uint16_t adc_value[ADC_COUNT] = { 0, };

// timer input capture flag and data
uint32_t ic_flag = 0;
int32_t ic_value[IC_CH_COUNT] = { 0, }; // microsecond
int32_t ic_buffer_0[IC_CH_COUNT] = { 0, };
int32_t ic_buffer_1[IC_CH_COUNT] = { 0, };

// accelerometer data
uint8_t acc_value[6];

// I2C transmission flag and buffer
uint32_t i2c_flag = 0;
ring_buffer_t ESP_BUFFER;
ring_buffer_t LCD_BUFFER;

// CAN RX header and data
CAN_RxHeaderTypeDef can_rx_header;
uint8_t can_rx_data[8];

// LCD update data
DISPLAY_DATA display_data;

// GPS receive flag and buffer
uint32_t gps_flag = 0;
uint8_t gps_data[1 << 7]; // 128B

/* USER CODE END PV */

void SystemClock_Config(void);
/* USER CODE BEGIN PFP */
int32_t ECU_SETUP(void);
/* USER CODE END PFP */

/* USER CODE BEGIN 0 */
int _write(int file, uint8_t *ptr, int len) {
  HAL_UART_Transmit(&huart1, (uint8_t *)ptr, (uint16_t)len, 50);
  return (len);
}
/* USER CODE END 0 */

/**
  * @brief  The application entry point.
  * @retval int
  */
int main(void)
{
  /* MCU Configuration--------------------------------------------------------*/

  /* Reset of all peripherals, Initializes the Flash interface and the Systick. */
  HAL_Init();

  /* Configure the system clock */
  SystemClock_Config();

  /* Initialize all configured peripherals */
  MX_GPIO_Init();
  MX_DMA_Init();
  MX_USART1_UART_Init();
  MX_I2C2_Init();
  MX_SDIO_SD_Init();
  MX_RTC_Init();
  MX_FATFS_Init();
  MX_ADC1_Init();
  MX_I2C1_Init();
  MX_CAN1_Init();
  MX_ADC2_Init();
  MX_USART2_UART_Init();
  MX_TIM1_Init();
  MX_I2C3_Init();
  MX_UART4_Init();
  MX_TIM3_Init();
  /* USER CODE BEGIN 2 */

  // check boot time
  int32_t ret;
  DATETIME boot;
  RTC_READ(&boot);

  #ifdef DEBUG_MODE
    printf("[%8lu] [INF] ECU STARTUP\r\n", HAL_GetTick());
  #endif

  // init ECU gpio and system state
  ret = ECU_SETUP();
  if (ret != 0) {
    #ifdef DEBUG_MODE
      printf("[%8lu] [ERR] ECU setup failed: %ld\r\n", HAL_GetTick(), ret);
    #endif
  } else {
    // core system boot complete
    syslog.value[0] = true;
    SYS_LOG(LOG_INFO, ECU, ECU_BOOT);
    #ifdef DEBUG_MODE
      printf("[%8lu] [ OK] ECU setup done\r\n", HAL_GetTick());
    #endif
  }

  // init SD card
  ret = SD_SETUP(&boot);
  if (ret != 0) {
    syslog.value[0] = false;
    SYS_LOG(LOG_ERROR, ECU, SD_INIT);
    #ifdef DEBUG_MODE
      printf("[%8lu] [ERR] SD setup failed: %ld\r\n", HAL_GetTick(), ret);
    #endif
  } else {
    syslog.value[0] = true;
    SYS_LOG(LOG_INFO, ECU, SD_INIT);
    #ifdef DEBUG_MODE
      printf("[%8lu] [ OK] SD setup done\r\n", HAL_GetTick());
    #endif
  }

  // init ESP32 i2c for remote telemetry
  ret = ESP_SETUP();
  if (ret != 0) {
    syslog.value[0] = false;
    SYS_LOG(LOG_ERROR, ESP, ESP_INIT);
    #ifdef DEBUG_MODE
      printf("[%8lu] [ERR] ESP setup failed: %ld\r\n", HAL_GetTick(), ret);
    #endif
  } else {
    syslog.value[0] = true;
    SYS_LOG(LOG_INFO, ESP, ESP_INIT);
    #ifdef DEBUG_MODE
      printf("[%8lu] [ OK] ESP setup done\r\n", HAL_GetTick());
    #endif
  }

  // init internal ADCs for sensors
  ret = ANALOG_SETUP();
  if (ret != 0) {
    syslog.value[0] = false;
    SYS_LOG(LOG_ERROR, ANALOG, ADC_INIT);
    HAL_GPIO_WritePin(GPIOE, ERR_SYS_Pin, GPIO_PIN_SET);
    #ifdef DEBUG_MODE
      printf("[%8lu] [ERR] ADC setup failed: %ld\r\n", HAL_GetTick(), ret);
    #endif
  } else {
    syslog.value[0] = true;
    SYS_LOG(LOG_INFO, ANALOG, ADC_INIT);
    #ifdef DEBUG_MODE
      printf("[%8lu] [ OK] ADC setup done\r\n", HAL_GetTick());
    #endif
  }

  // init CAN for BMS and inverter
  ret = CAN_SETUP();
  if (ret != 0) {
    syslog.value[0] = false;
    SYS_LOG(LOG_ERROR, CAN, CAN_INIT);
    HAL_GPIO_WritePin(GPIOE, ERR_CAN_Pin, GPIO_PIN_SET);
    #ifdef DEBUG_MODE
      printf("[%8lu] [ERR] CAN setup failed: %ld\r\n", HAL_GetTick(), ret);
    #endif
  } else {
    syslog.value[0] = true;
    SYS_LOG(LOG_INFO, CAN, CAN_INIT);
    #ifdef DEBUG_MODE
      printf("[%8lu] [ OK] CAN setup done\r\n", HAL_GetTick());
    #endif
  }

  // init 1602 LCD i2c
  ret = LCD_SETUP();
  if (ret != 0) {
    syslog.value[0] = false;
    SYS_LOG(LOG_ERROR, LCD, LCD_INIT);
    HAL_GPIO_WritePin(GPIOE, ERR_SYS_Pin, GPIO_PIN_SET);
    #ifdef DEBUG_MODE
      printf("[%8lu] [ERR] LCD setup failed: %ld\r\n", HAL_GetTick(), ret);
    #endif
  } else {
    syslog.value[0] = true;
    SYS_LOG(LOG_INFO, LCD, LCD_INIT);
    #ifdef DEBUG_MODE
      printf("[%8lu] [ OK] LCD setup done\r\n", HAL_GetTick());
    #endif
  }

  // init ADXL345 3-axis accelerometer i2c
  ret = ACC_SETUP();
  if (ret != 0) {
    syslog.value[0] = false;
    SYS_LOG(LOG_ERROR, ACC, ACC_INIT);
    HAL_GPIO_WritePin(GPIOE, ERR_SYS_Pin, GPIO_PIN_SET);
    #ifdef DEBUG_MODE
      printf("[%8lu] [ERR] ACC setup failed: %ld\r\n", HAL_GetTick(), ret);
    #endif
  } else {
    syslog.value[0] = true;
    SYS_LOG(LOG_INFO, ACC, ACC_INIT);
    #ifdef DEBUG_MODE
      printf("[%8lu] [ OK] ACC setup done\r\n", HAL_GetTick());
    #endif
  }

  // init NEO-7M GPS UART
  ret = GPS_SETUP();
  if (ret != 0) {
    syslog.value[0] = false;
    SYS_LOG(LOG_ERROR, GPS, GPS_INIT);
    HAL_GPIO_WritePin(GPIOE, ERR_SYS_Pin, GPIO_PIN_SET);
    #ifdef DEBUG_MODE
      printf("[%8lu] [ERR] GPS setup failed: %ld\r\n", HAL_GetTick(), ret);
    #endif
  } else {
    syslog.value[0] = true;
    SYS_LOG(LOG_INFO, GPS, GPS_INIT);
    #ifdef DEBUG_MODE
      printf("[%8lu] [ OK] GPS setup done\r\n", HAL_GetTick());
    #endif
  }

  // start hardware timers
  HAL_TIM_Base_Start_IT(&htim1);

  // system setup sequence complete
  syslog.value[0] = true;
  SYS_LOG(LOG_INFO, ECU, ECU_READY);
  #ifdef DEBUG_MODE
    printf("[%8lu] [INF] ECU READY\r\n", HAL_GetTick());
  #endif

  /* USER CODE END 2 */

  /* Infinite loop */
  /* USER CODE BEGIN WHILE */

  while (1) {

    // CPU temmperature ADC conversion done
    if ((adc_flag & (1 << ADC_CPU)) != 0) {
      adc_flag &= ~(1 << ADC_CPU); // clear ADC_CPU flag
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

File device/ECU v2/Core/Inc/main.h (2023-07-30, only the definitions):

#define LED00_Pin GPIO_PIN_6
#define LED00_GPIO_Port GPIOA
#define LED01_Pin GPIO_PIN_7
#define LED01_GPIO_Port GPIOA
#define ERR_SYS_Pin GPIO_PIN_10
#define ERR_SYS_GPIO_Port GPIOE
#define ERR_CAN_Pin GPIO_PIN_11
#define ERR_CAN_GPIO_Port GPIOE
#define LED_HEARTBEAT_Pin GPIO_PIN_12
#define LED_HEARTBEAT_GPIO_Port GPIOE
#define LED_SD_Pin GPIO_PIN_13
#define LED_SD_GPIO_Port GPIOE
#define LED_CAN_Pin GPIO_PIN_14
#define LED_CAN_GPIO_Port GPIOE
#define LED_ESP_Pin GPIO_PIN_15
#define LED_ESP_GPIO_Port GPIOE
#define SDIO_DETECT_Pin GPIO_PIN_12
#define SDIO_DETECT_GPIO_Port GPIOB
#define RTD_ACTIVE_Pin GPIO_PIN_10
#define RTD_ACTIVE_GPIO_Port GPIOD
#define HV_ACTIVE_Pin GPIO_PIN_11
#define HV_ACTIVE_GPIO_Port GPIOD
#define BMS_FAULT_Pin GPIO_PIN_12
#define BMS_FAULT_GPIO_Port GPIOD
#define IMD_FAULT_Pin GPIO_PIN_13
#define IMD_FAULT_GPIO_Port GPIOD
#define BSPD_FAULT_Pin GPIO_PIN_14
#define BSPD_FAULT_GPIO_Port GPIOD

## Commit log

2022-08-10 FIX: char to uint8_t
    [main.c]
2022-08-10 FIX: ECU Error_Handler null character bug
    [main.c]
2022-08-11 ADD: ECU accelerometer
2022-08-12 ADD: ECU accelerometer support
2022-08-18 FIX: some bugs on ECU
    [ECU.ioc, main.c, main.h]
2022-08-20 FIX: CAN baud rate to 250kbps
    [ECU.ioc, can.c]
2022-08-21 FIX: UART transmit timeout
    [ECU.ioc, ESP.ino, main.c]
2022-10-03 ADD: corner weight measurement
    [2-1445088-8.step, BATT_PCB.kicad_sch, BSPD.kicad_sch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]
2022-10-03 FIX: ECU UART timeout
    [ECU.ioc, can.c, main.c]
2022-11-14 Project location moved
    [2-1445088-8.step, BATT_PCB.kicad_sch, BSPD.kicad_sch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]
2023-02-19 add ADC support
2023-02-19 fix timer prescaled and period
    [ECU v2.ioc, main.c, tim.c]
2023-02-21 change timer period & ring buffer manipulation
2023-02-21 implement i2c tx buffer prototype
2023-02-21 fix misc missing codes
    [i2c.c, logger.c, main.c]
2023-02-23 add accelerometer support
2023-02-24 CAN prototype
2023-02-25 add CAN filter support
2023-02-25 add GPS prototype
2023-02-26 add GPS support and ADC optimization
2023-02-26 fix wrong ADC log key
2023-02-28 add ESP i2c transmit prototype
2023-02-28 ESP32 RTC sync prototype
2023-03-20 add: TIM5 for input capture with DMA
2023-04-05 fix: input capture timer frequency to 1Hz
    [ECU v2.ioc, main.c, tim.c]
2023-04-05 add: tim ic dma prototype
2023-04-11 add: tim ic dma logic
2023-06-04 add: esp32 socket & time sync prototype
2023-06-05 fix: stack overflow on ESP
    [ESP_v2.ino]
2023-06-22 update: i2c log transmit
2023-06-24 fix: inverted state for HV and RTD
    [main.c]
2023-06-25 update: accelerometer g calculation
2023-06-26 update: linear position sensor value calculation
2023-06-26 add: stm32 heartbeat led
2023-06-27 add: gps track feature
2023-06-30 update: timer input capture log name
2023-06-30 improve: timer input capture logic
2023-07-27 rename: LED2 to HEARTBEAT
2023-07-30 add: ERR_SYS LED
2023-07-30 add: ERR_CAN LED support
2023-07-31 fix: LCD I2C freq 50kHz from 400kHz
    [ECU v2.ioc, i2c.c]
2023-08-16 fix: linear distance sensor logging interval bug
    [main.c]
2023-08-17 fix: wrong linear sensor channel
    [ECU v2.ioc, adc.c, main.c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]
2023-08-20 update: 10kHz LCD I2C freq

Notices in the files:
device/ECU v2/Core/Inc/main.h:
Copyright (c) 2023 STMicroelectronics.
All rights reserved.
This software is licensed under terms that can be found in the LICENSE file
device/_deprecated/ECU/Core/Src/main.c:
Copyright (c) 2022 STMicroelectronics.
